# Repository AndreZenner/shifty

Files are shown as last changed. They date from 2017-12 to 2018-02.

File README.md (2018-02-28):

# Shifty
This repository allows you to build your own **Shifty** - a weight-shifting dynamic passiv haptic proxy for virtual reality!

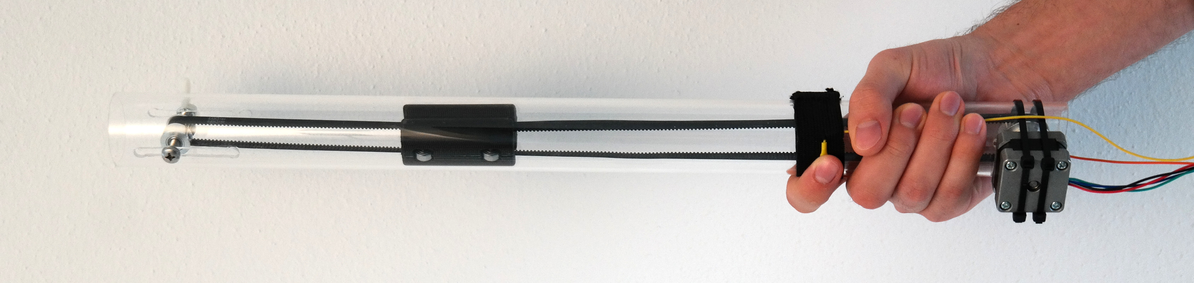
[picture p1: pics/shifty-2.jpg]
Image of the Shifty prototype The Shifty prototype


## Introduction
**Shifty**, as introduced in our TVCG paper [Shifty: A Weight-Shifting Dynamic Passive Haptic Proxy to Enhance Object Perception in Virtual Reality](https://doi.org/10.1109/TVCG.2017.2656978 "Shifty @ IEEE Xplore Digital Library") is a weight-shifting VR controller that allows you to better feel the weight of virtual objects and transformations of them.
For this, it shifts an internal mass while you interact with virtual objects in VR.
Using appropriate visualizations in the virtual environment in synchronization with Shifty's changes in mass distribution (and thus the felt moment of inertia and lever arm), allows for immersive haptic experiences in VR. 

For more information on its haptic effect, the scientific background and user study results, please take a look at the paper.
Shifty was presented at the [IEEE Virtual Reality Conference 2017 in Los Angeles](https://youtu.be/Tzx6ZOIjLhY "Watch the talk!").
To get a first impression, the [corresponding video](https://youtu.be/1l0wKk6q_ss "Watch the video!") is probably a good starting point.

## Reference
```
@article{Zenner:2017:Shifty,
  title={Shifty: A Weight-Shifting Dynamic Passive Haptic Proxy to Enhance Object Perception in Virtual Reality},
  author={Zenner, Andr{\'e} and Kr{\"u}ger, Antonio},
  journal={IEEE Transactions on Visualization and Computer Graphics},
  volume={23},
  number={4},
  pages={1285--1294},
  year={2017},
  publisher={IEEE},
  doi={10.1109/TVCG.2017.2656978}
}
```

## Contents
This repository contains the files, source code and information you need to make your own Shifty prototype.

- [3d-prints](3d-prints/) contains the files to 3D print 
  - Shifty's internal weight hull (you have to fill it with lead granulate)
  - A mount for the HTC Vive tracker (you have to get a 1/4" camera screw) that can be plugged on Shifty
- [circuit](circuit/) contains the [Fritzing](http://fritzing.org/home/) file and a drawing of the used Arduino circuit
- [laser-cut](laser-cut/) contains the .svg cutter file to cut the box holding the electronics
- [pics](pics/) contains pictures of parts, intermediate building steps and the final prototype
- [src](src/) contains the source code
  - [src/arduino](src/arduino/) holds the Arduino firmware to deploy on the Arduino Uno, handling WiFi communication and motor control
  - [src/api](src/api/) holds the C# API that allows programs to talk to Shifty's Arduino and that can be used to control the weight shift and receive button presses. As configured, this Visual Studio project currently builds a .dll to include in your own programs (e.g. used in Unity to communicate with Shifty)
  - [src/unity](src/unity/) holds a small minimal-example project that demonstrates how to integrate the API in Unity using the .dll file (Unity 5.6)
  
## Parts you need
You will probably need the following parts to build the prototype:
- Power:
  - charger for 12V rechargeable battery
  - 12V rechargeable battery (we used a lead accumulator with 7.2 Ah and 6.3mm connectors)
  - DC 12V Step Up Step Down Converter
  - 2x On-Off switch
- Mechanics:
  - plexiglas	pipe outer-Ø: 40,0mm, inner-Ø: 36,0mm
  - Nema 14 Step Motor 12V 0.4A 14Ncm/20oz.in 35x35x26mm 1.8deg Bipolar 4-wire
  - small pulley (GT2 Pulley, 20 teeth, Ø8mm, gear)
  - big pulley (GT2 Pulley, 40 teeth, Ø5mm, gear)
  - toothed belt (GT2)
  - ball bearings for small pulley 5x8x2,5mm
  - ball bearings for weight-wheels 6x12x4mm
  - M5 screw
  - M5 wing nut
  - cable ties for the motor
  - rubberband 25mm width to hold the button
  - velcro strap to fix the rubberband holding the button
  - fine lead granulate ø 0,6 - 1,5 mm
  - backpack to put the battery and electronics in
- Electronics:
  - Arduino Uno R3
  - Adafruit Motor/Stepper/Servo Shield for Arduino Version 2.3
  - Adafruit stacking header set
  - ESP8266 WiFi Module
  - Mini-Breadboard - 400 contacts
  - Mini-Button, placed on Shifty with the rubberband (e.g. SMD Button 3x6x2.5mm)
  - capacitors (104, 100nF)
  - resistors as shown in the circuit schematics
  - LED as shown in the circuit schematics 
  - Buzzer 5V / 12mm
  - shielded microphone cable (4 x 0.14 mm²)
  - connector (8-pin)
  - some jumper wires
  
Additionally, to make the weight and the Vive Tracker mount, you will need access to a 3D printer (we used an Ultimaker 2+; PLA) and to laser-cut the box, access to a laser cutter.

## How-To Build
To build a Shifty prototype, follow these steps:

### Prepare the ESP8266 WiFi chip
We used the ESP8266 module with AT version 0.18 - as it works with the [WeeESP8266](https://github.com/itead/ITEADLIB_Arduino_WeeESP8266) Arduino library. For this to work, you need the corresponding firmware running on your ESP module. To flash the firmware on the module, you can use the [esptool](https://github.com/themadinventor/esptool) and follow [this video](https://www.youtube.com/watch?v=PycRnjcXMRI). A working firmware to flash can be found [here](http://wiki.fablab-nuernberg.de/w/Ding:ESP8266#Firmware) (click V0.9.2.4).
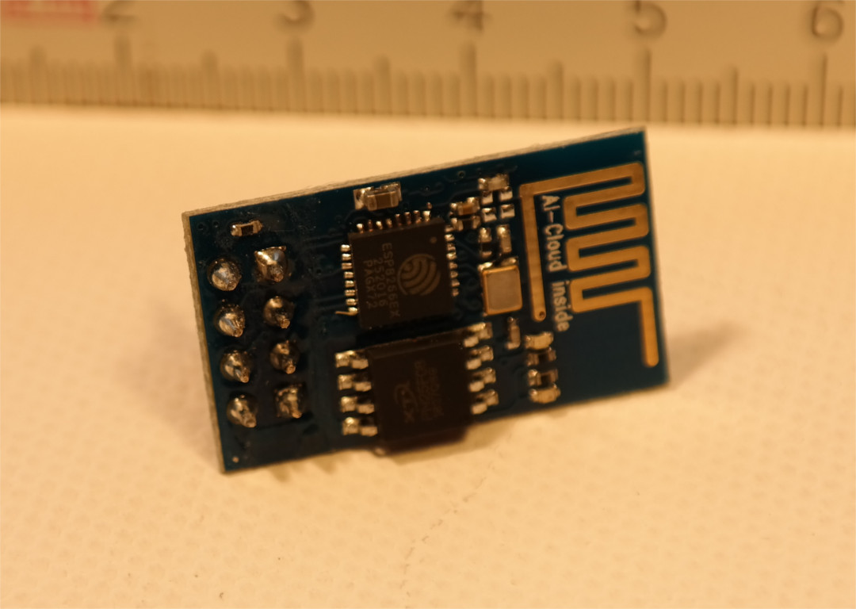
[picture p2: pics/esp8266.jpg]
The ESP8266 WiFi module


### Building Shifty
Having all required parts ready, you can build the prototype:
#### Step 1: Pipe, Motor, Pulley
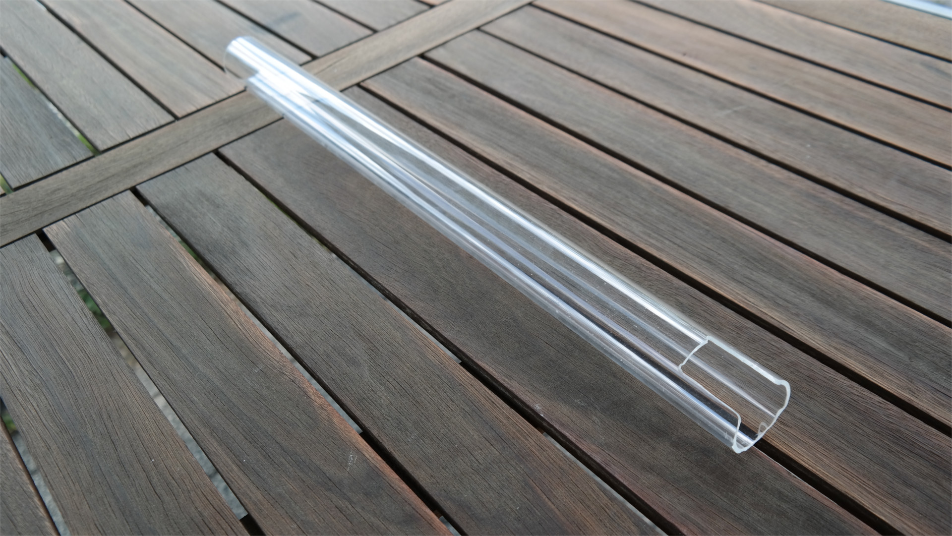
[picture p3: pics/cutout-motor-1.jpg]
motor cutout w/o motor
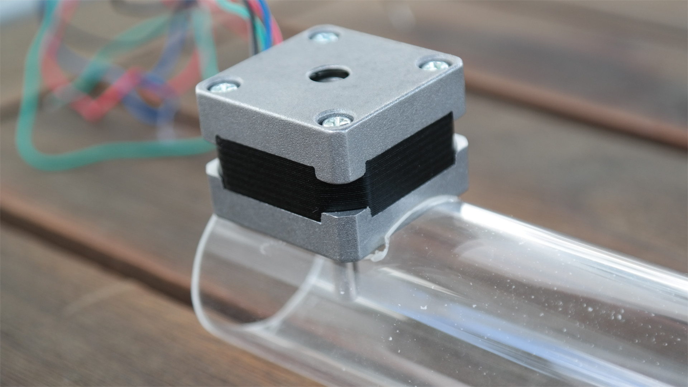
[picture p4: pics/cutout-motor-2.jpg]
motor cutout w/ motor
1. Take the plexiglas pipe, cut it in the desired proxy length and make a cutout for the motor to reside on  
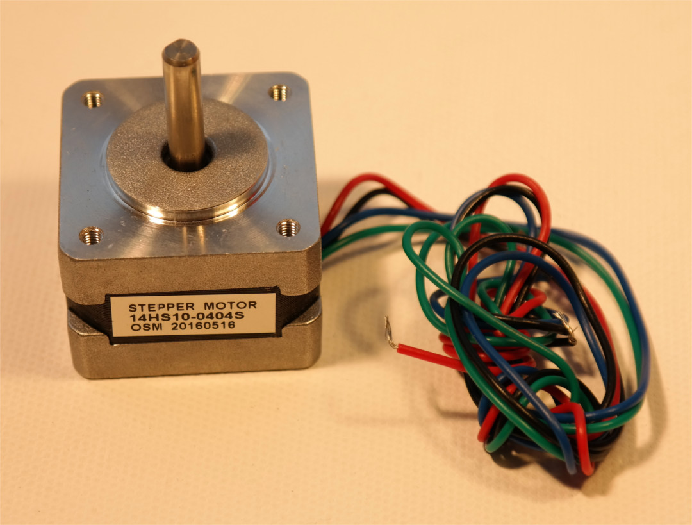
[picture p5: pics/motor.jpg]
motor
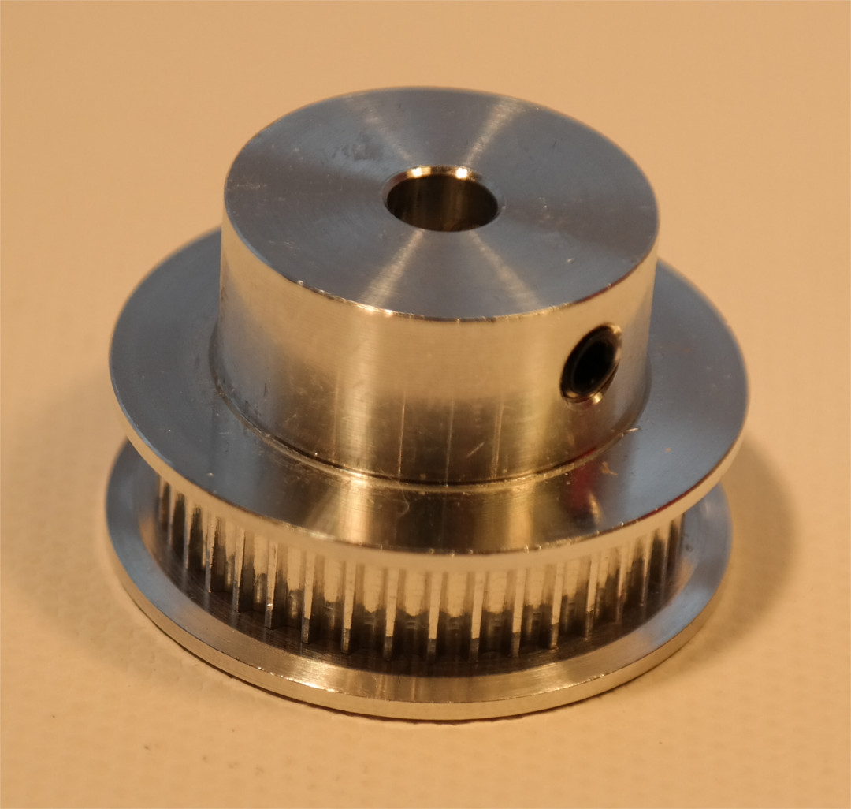
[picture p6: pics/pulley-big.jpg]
big pulley
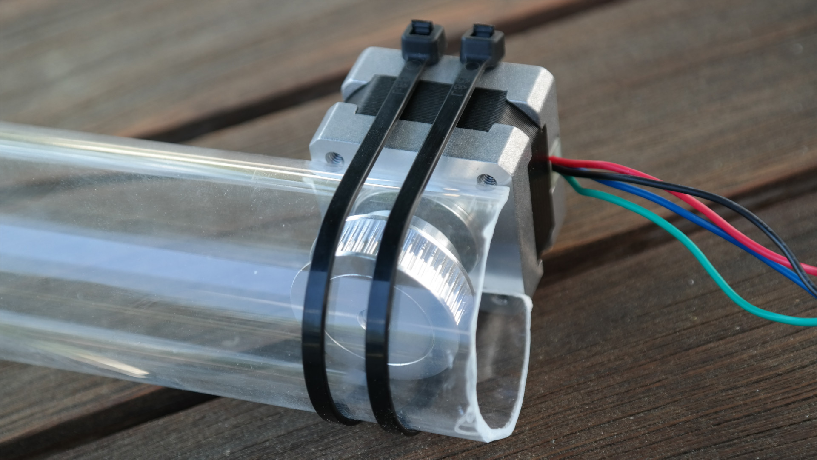
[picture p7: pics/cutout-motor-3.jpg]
motor fixed
2. Using the cable ties, fix the motor with the big pulley screwed on the shaft, so that the pulley is exactly in the center of the pipe. You can put leather between pipe and motor to dampen vibrations and sound.   
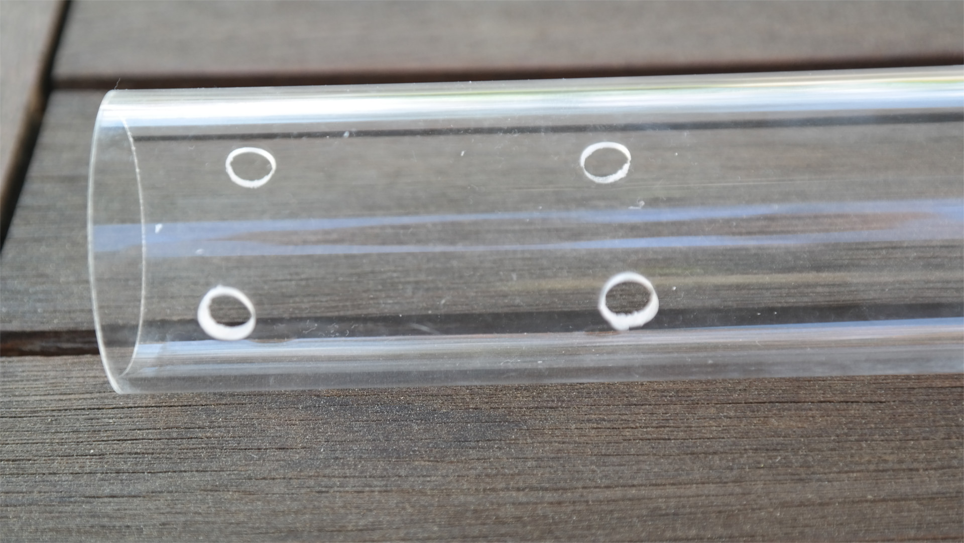
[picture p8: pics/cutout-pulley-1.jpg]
pulley cutout holes
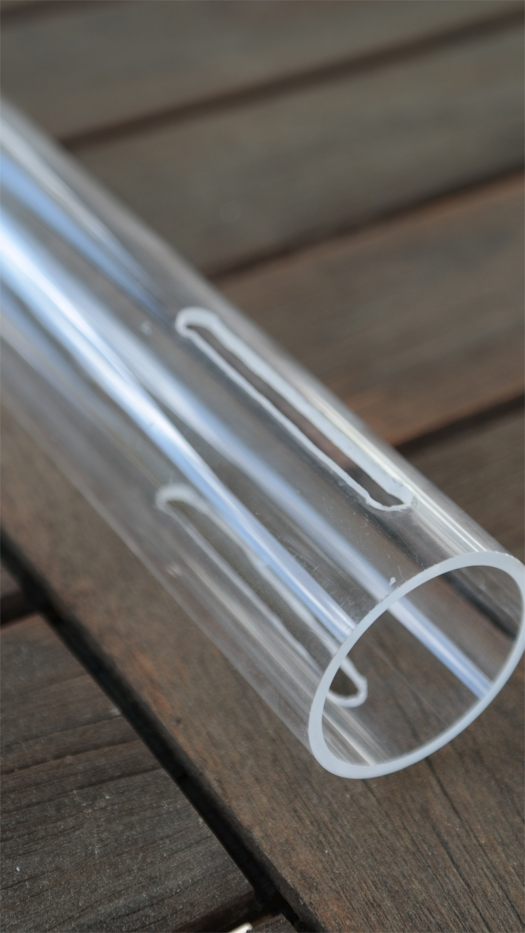
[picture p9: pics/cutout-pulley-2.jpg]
pulley cutout
3. On the other end of the pipe, cut two lengthy recesses for the M5 screw (e.g. by drilling holes and connecting them using a Dremel) 
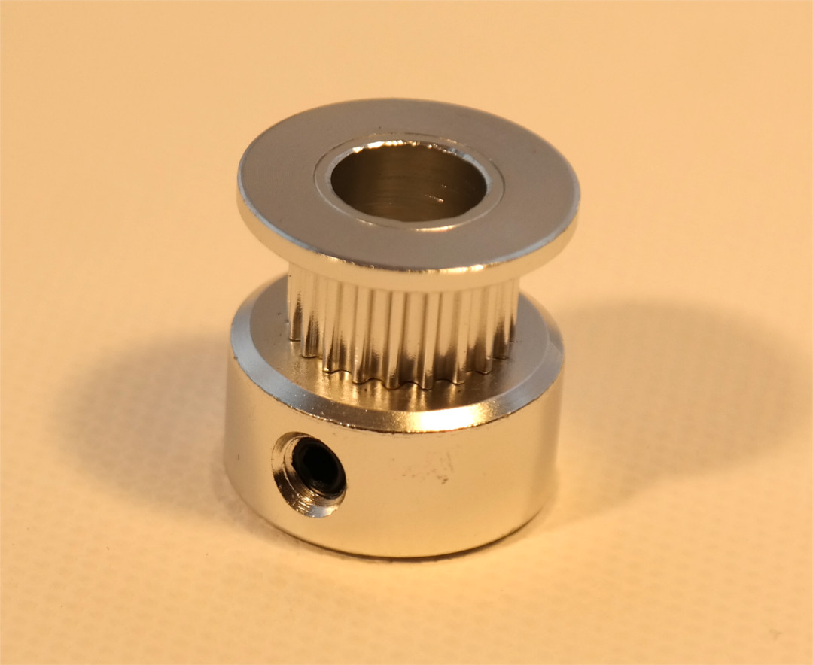
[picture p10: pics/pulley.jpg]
small pulley
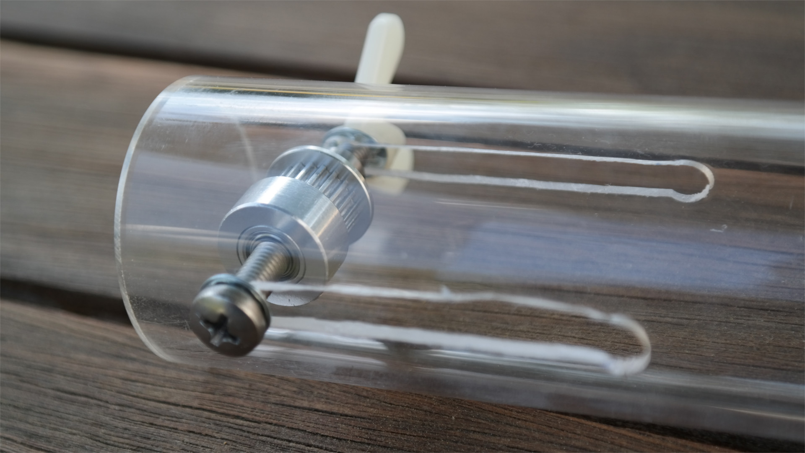
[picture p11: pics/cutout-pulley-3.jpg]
pulley fixed
4. Take the screw, put the small pulley with the ball bearings on it and insert it into the pipe through the recesses. Fix it with the wing nut. 

#### Step 2: Weight, Belt
1. Print the weight hull two times with a 3D printer
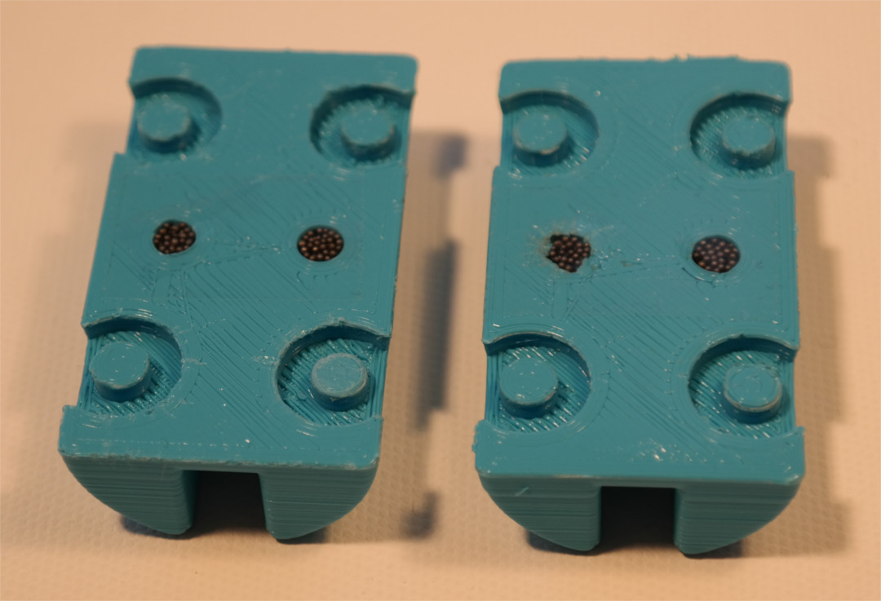
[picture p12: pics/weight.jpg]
2. Fill both halves with the lead granulate 
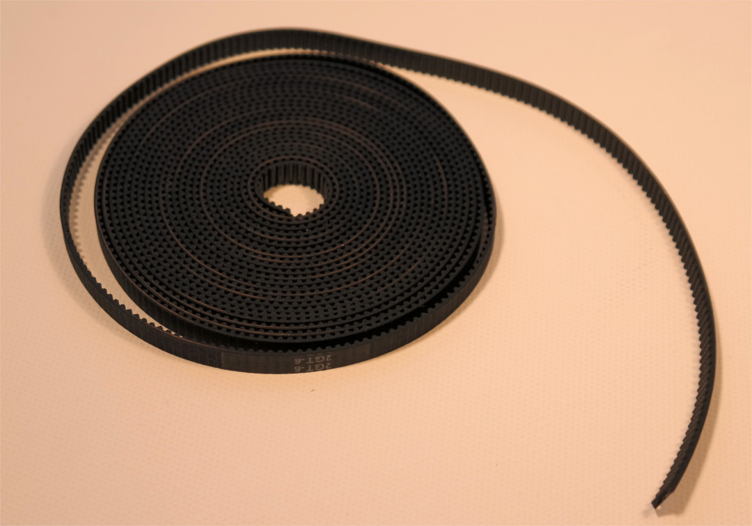
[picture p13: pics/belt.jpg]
belt
3. Measure the distance between the big pulley on the motor and the small pulley on the top end of the pipe to determine the length of the belt. Then cut the belt. 
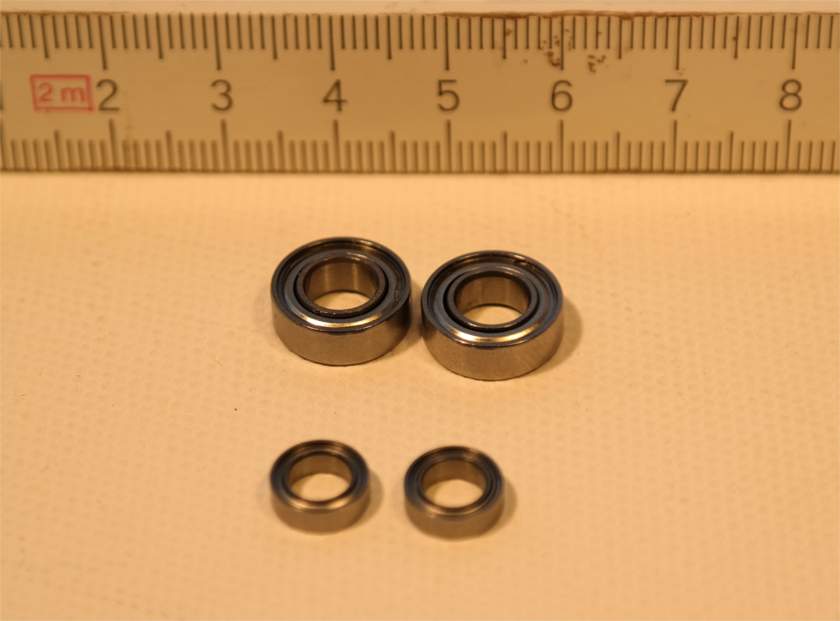
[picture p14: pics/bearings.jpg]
bearings
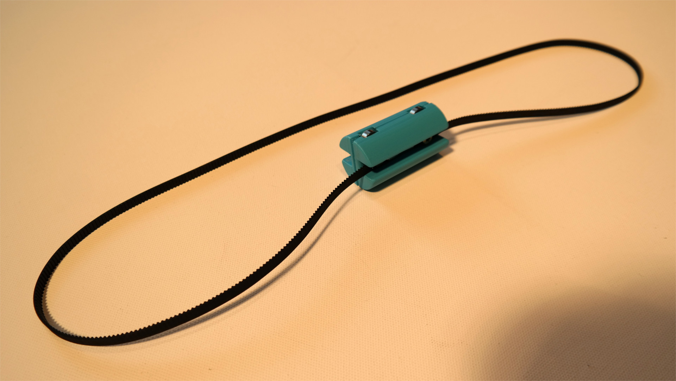
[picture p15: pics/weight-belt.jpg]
assembled weight attached to belt
4. Insert the bearings as weight-wheels and fix the two weight halves. Then attach the belt on the weight.  

#### Step 3: Button
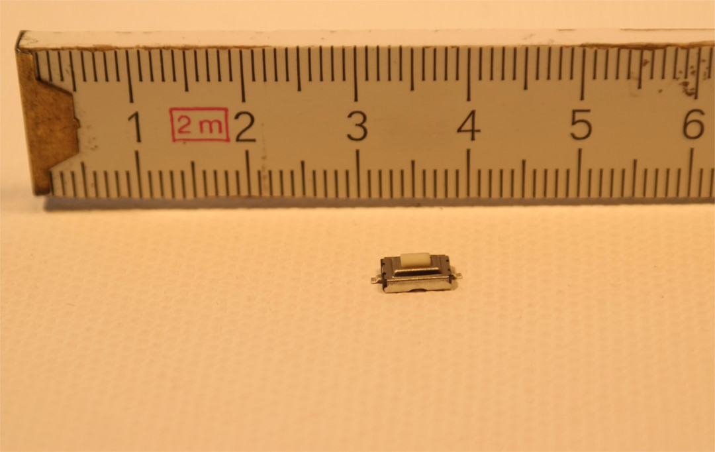
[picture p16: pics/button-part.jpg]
small button
1. Take the small button and attach a cable on both ends. 
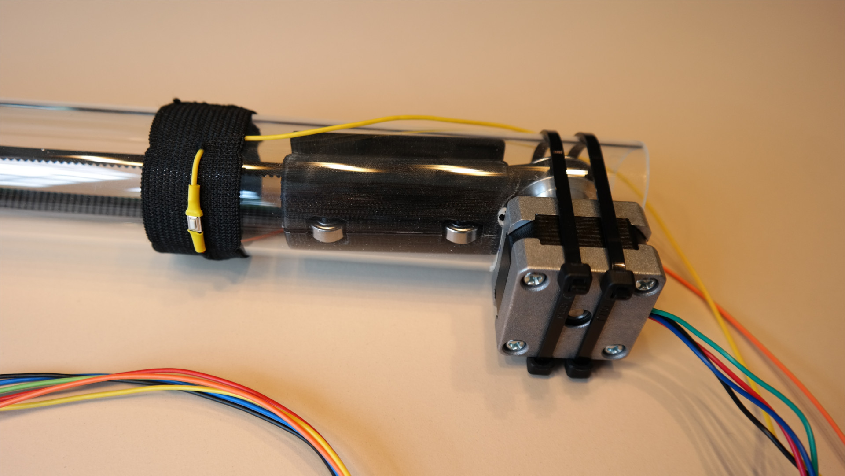
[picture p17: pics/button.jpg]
button fixed with rubberband on Shifty
2. Cut the rubberband and the velcron strap. Stick the two cables through the band in order to attach the button on the pipe. 

#### Step 4: Arduino, Circuit, Cables
1. Prepare the ESP8266 module as described above.
2. Solder the stacking headers to the motor shield and stack the shield on the Arduino.
3. Create the circuit. Shifty circuit
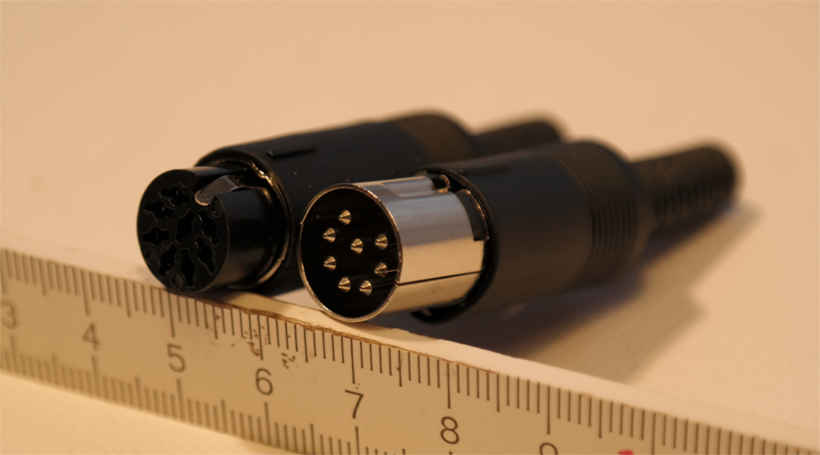
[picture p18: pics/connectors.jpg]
connectors
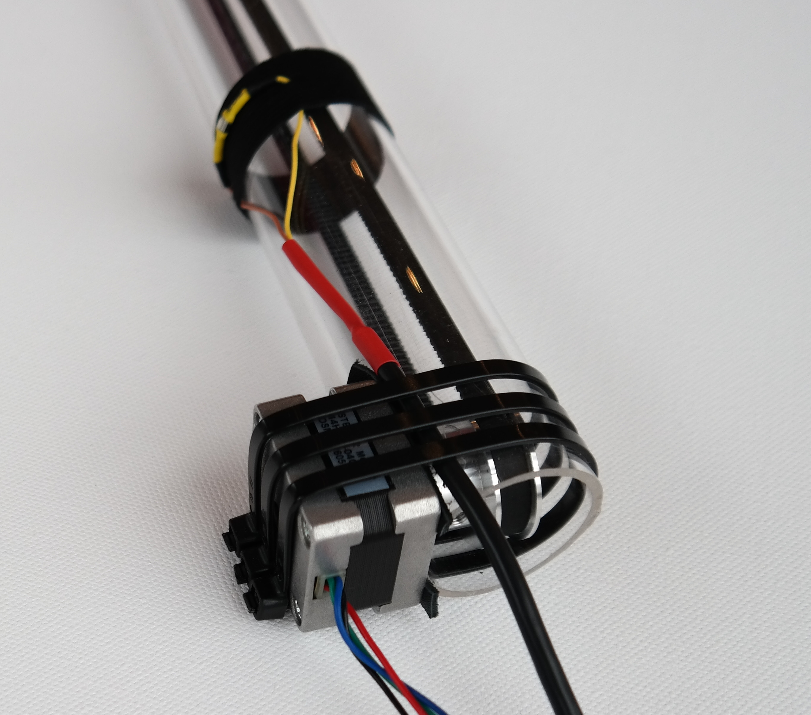
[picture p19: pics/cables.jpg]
cables at Shifty
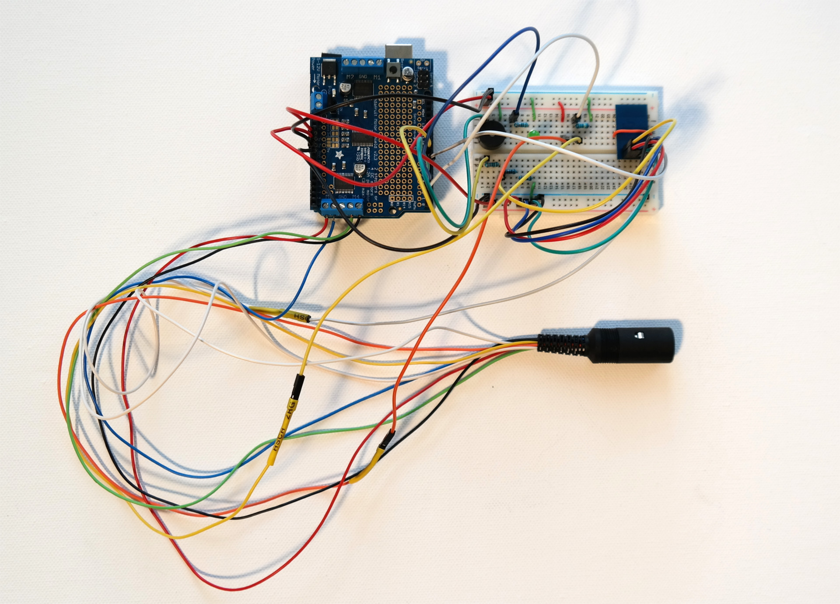
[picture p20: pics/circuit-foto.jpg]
photo of the curcuit
4. Solder the cable connections and connectors. <p>The electronics should look like this:</p>
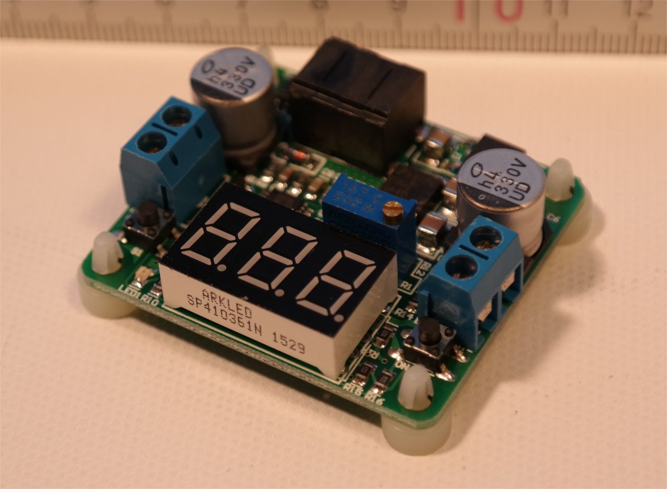
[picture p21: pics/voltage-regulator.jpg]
voltage converter
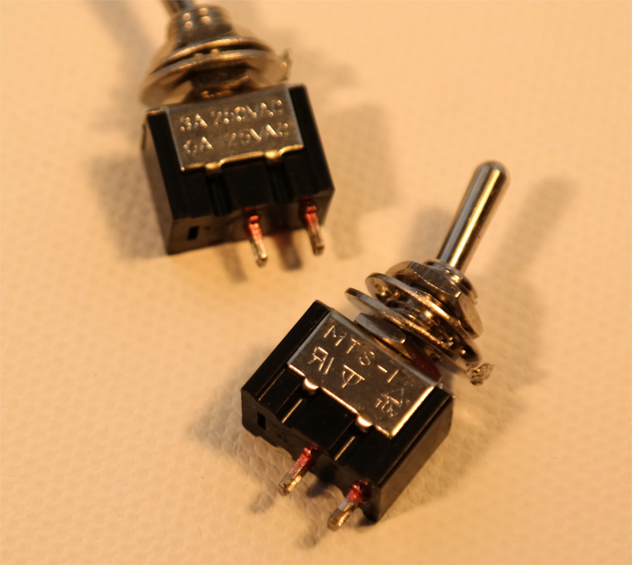
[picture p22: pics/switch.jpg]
switches
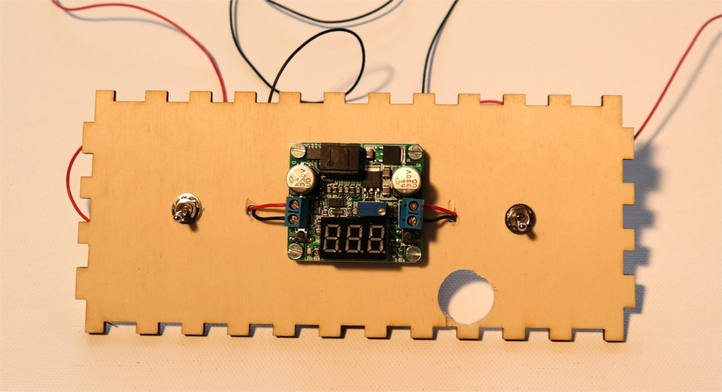
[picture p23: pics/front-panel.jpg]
front panel
5. Using the voltage converter and switches, prepare the power supply (e.g. on the font panel of the box)   

#### Step 5: Final Assembly, Vive Tracker Mount
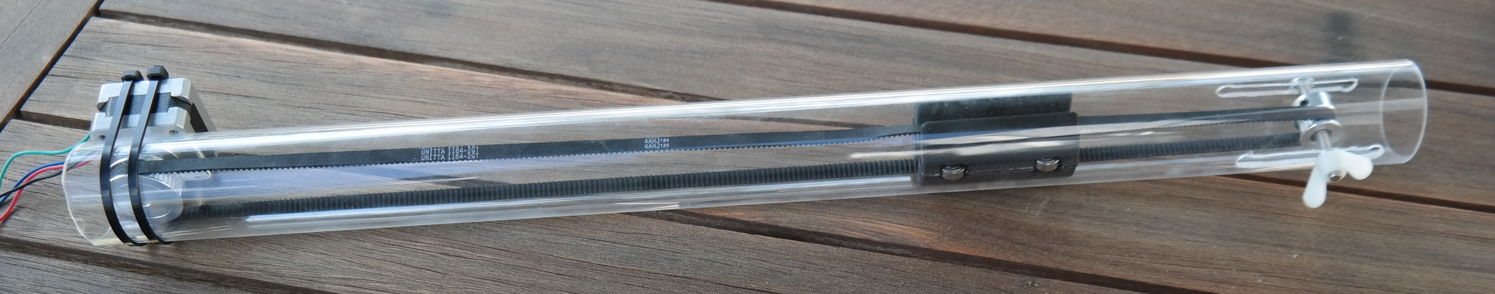
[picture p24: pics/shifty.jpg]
shifty with inserted weight
1. Insert the weight and the belt in the pipe. Fasten the belt by adjusting the position of the top pulley / screw. 
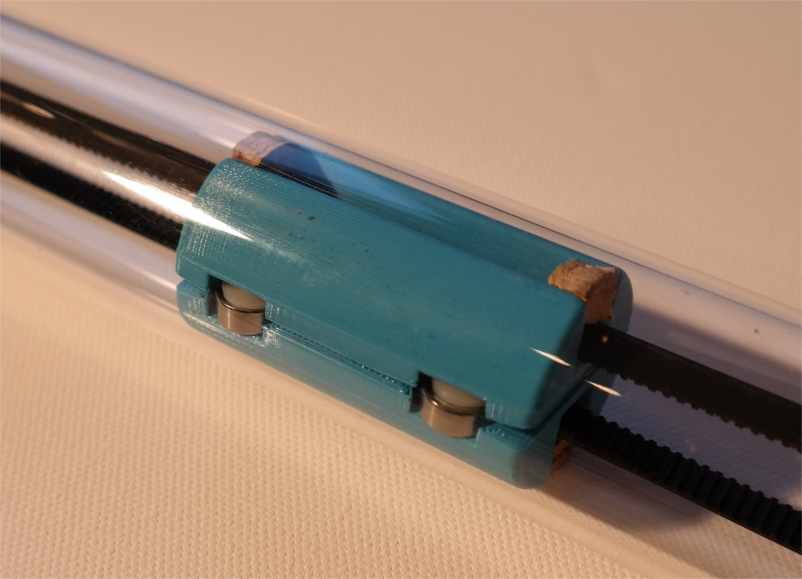
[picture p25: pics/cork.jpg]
cork on the weight
2. If too loud, you can use small pieces of cork to dampen the sound of the internal weight. 
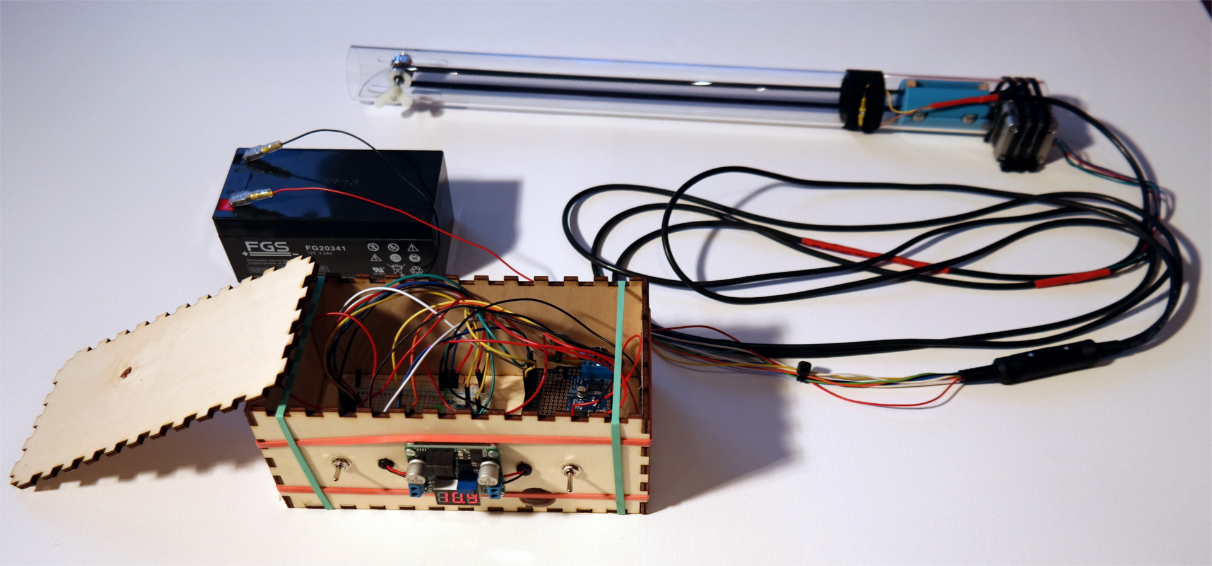
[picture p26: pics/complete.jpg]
complete Shifty prototype
3. Putting everything together, the result should look similar to this: 
4. Deploy the [Shifty Arduino software](src/arduino/) on the Arduino and test if it works. After start-up, Shifty has to be calibrated. For this, the weight will automatically move towards the top and you have to press the button at the top-most end. After that, the weight moves downwards and you have to set the lowest position again by pressing the button. Upon completion of this calibration, Shifty is ready to go!
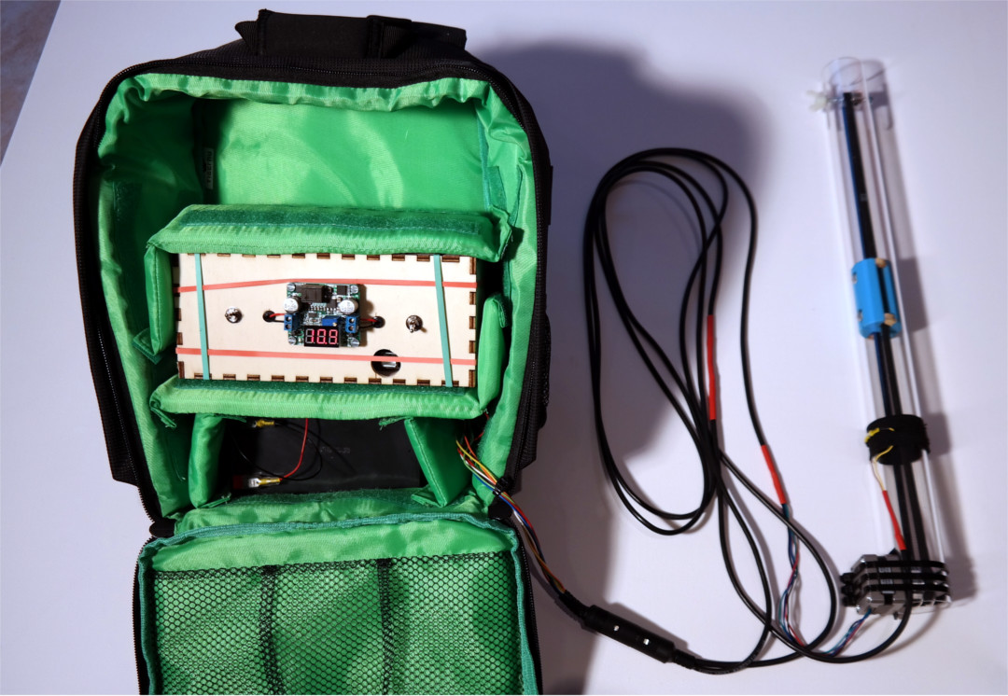
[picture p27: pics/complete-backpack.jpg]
complete Shifty prototype with backpack
5. If everything works, take a backpack and insert the battery and the electronics with the box, just leaving a cable connection to Shifty. Wearing the backback, you can use Shifty even in room-scale VR experiences. 
6. Finally, 3D print the Vive Tracker mount and place the tracker on Shifty to easily track it while in VR.

#### Step 6: Useful Addons
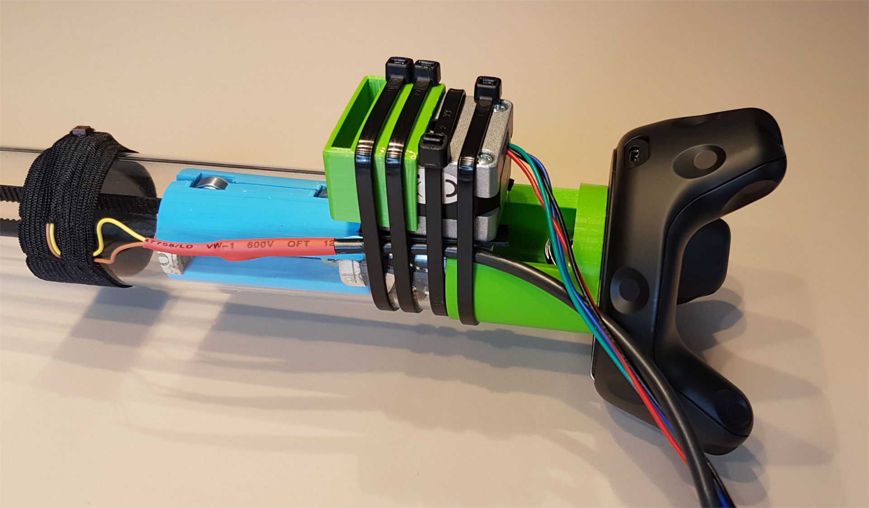
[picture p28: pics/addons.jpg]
3D printed addons

1. For better balance and more ergonomic placement of the Vive tracker, 3D print the grip mount and fix it at the grip end with a cable tie. Screw the Vive tracker with a camera screw.
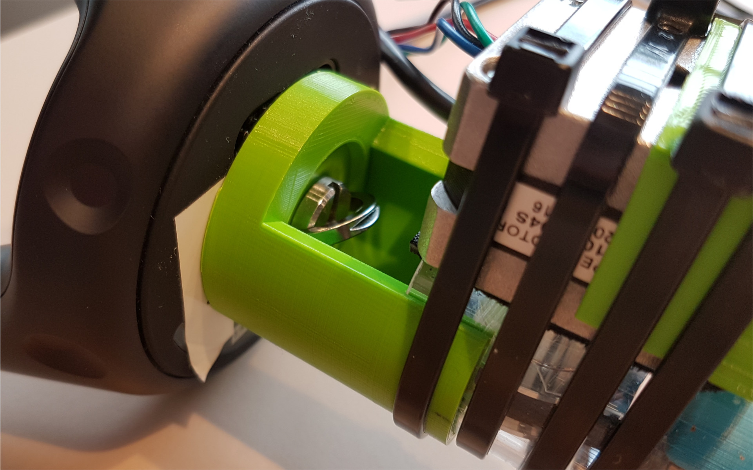
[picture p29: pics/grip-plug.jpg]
the grip mount for the Vive tracker

2. As the motor can become very hot, you should use a heat shield to prevent burning your hand when touching the motor while in VR. For this, you can 3D print the heat shield file and fix it on the motor with additional cable ties.
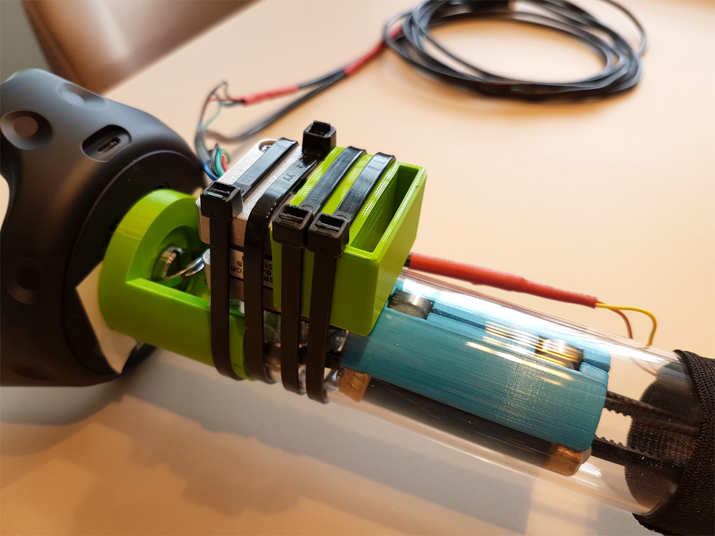
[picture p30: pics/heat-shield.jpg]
heat shield mounted on the motor


### Controlling Shifty
Use the [ProxyControlAPI](src/api/) to connect to Shifty, to pass commands and to read the button states.
The library currently builds a .dll file containing the API functions.
See the [Unity Example](src/unity/), and especially the corresponding [ExampleProxyConnection.cs](src/unity/Shifty-Unity-Minimal-Example/Assets/github-minimal/ExampleProxyConnection.cs) script, as well as the functions offered by the API defined in [ProxyControlAPI.cs](src/api/ProxyControlAPI/ProxyControlClient/ProxyControlAPI.cs), for examples and reference.

To test your prototype, you can build and use the small [ProxyControlAPI-Console tool](src/api/ProxyControlAPI/) that allows you to send commands manually in order to test your device.

## Credits
Before use, please see the [LICENSE](LICENSE.md) for copyright and license details.

Authors of the [paper](https://doi.org/10.1109/TVCG.2017.2656978 "Shifty @ IEEE Xplore Digital Library"):  
**André Zenner** - andre.zenner@dfki.de  
**Prof. Dr. Antonio Krüger** - krueger@dfki.de

This work was supported by the [Deutsches Forschungszentrum für Künstliche Intelligenz GmbH](https://www.dfki.de/) (DFKI; German Research Center for Artificial Intelligence) and [Saarland University](https://www.uni-saarland.de/).
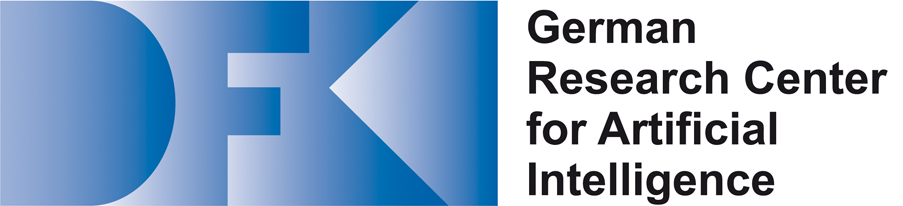
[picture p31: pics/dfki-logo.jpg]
DFKI Logo

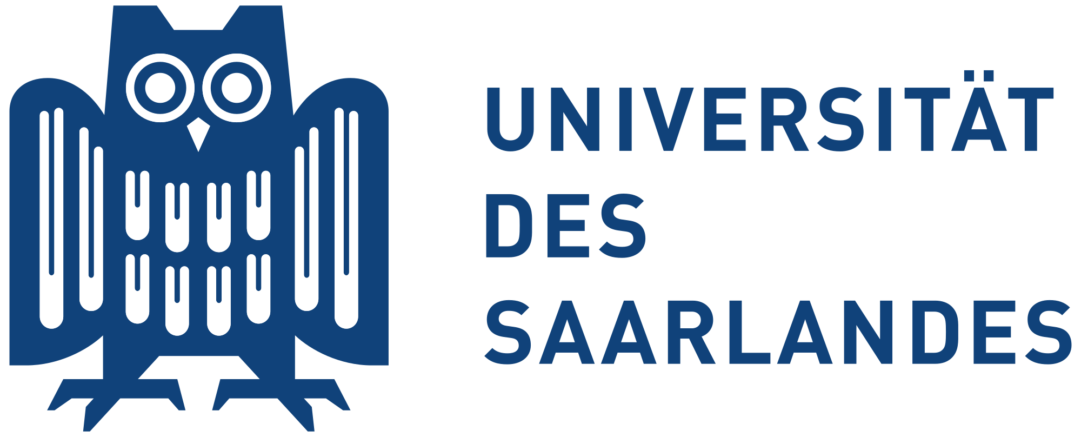
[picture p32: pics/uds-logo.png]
Saarland University Logo


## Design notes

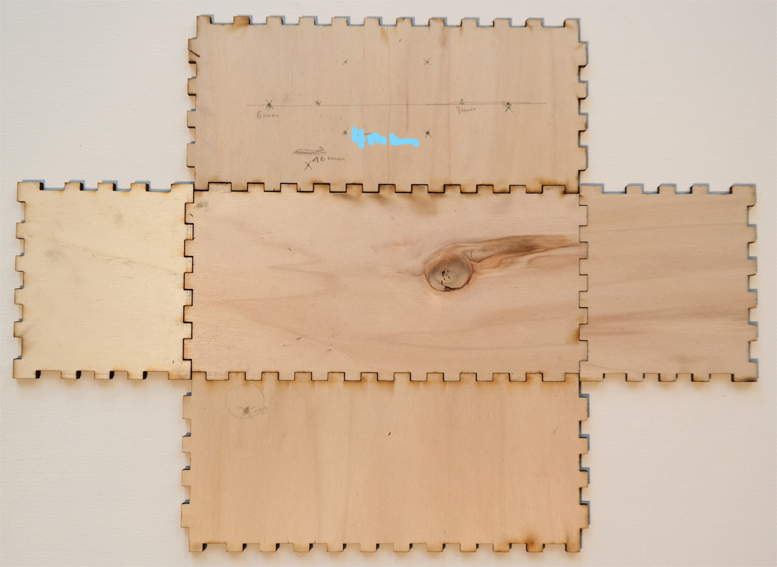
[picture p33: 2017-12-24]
pics/box-1.jpg

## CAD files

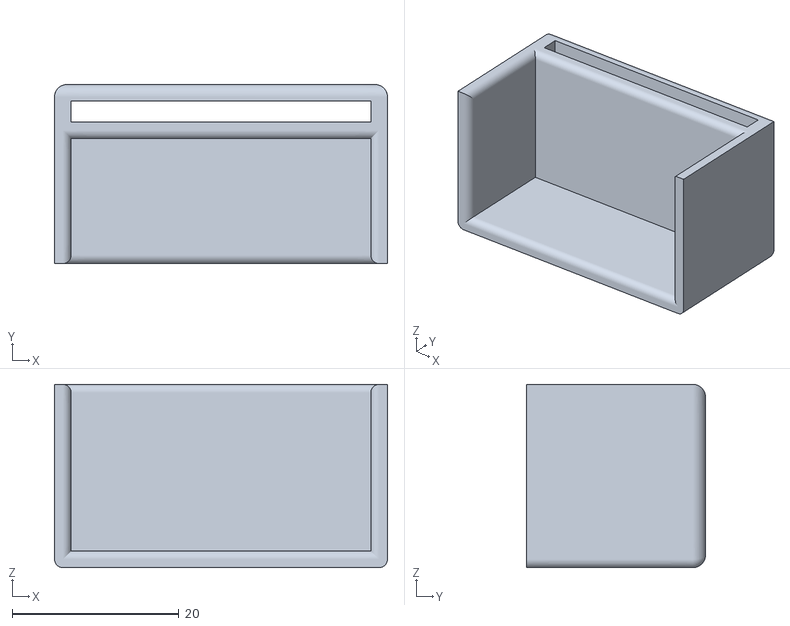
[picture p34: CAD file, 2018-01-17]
3d-prints/v2-Shifty-Heat-Shield.stl
40.0 x 21.5 x 22.0

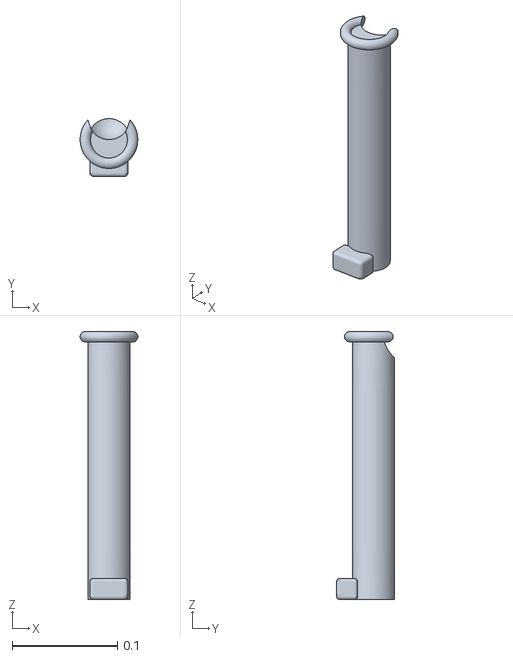
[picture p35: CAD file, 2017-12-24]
src/unity/Shifty-Unity-Minimal-Example/Assets/VirtualObjects/grip1.obj
0.0549 x 0.055 x 0.255

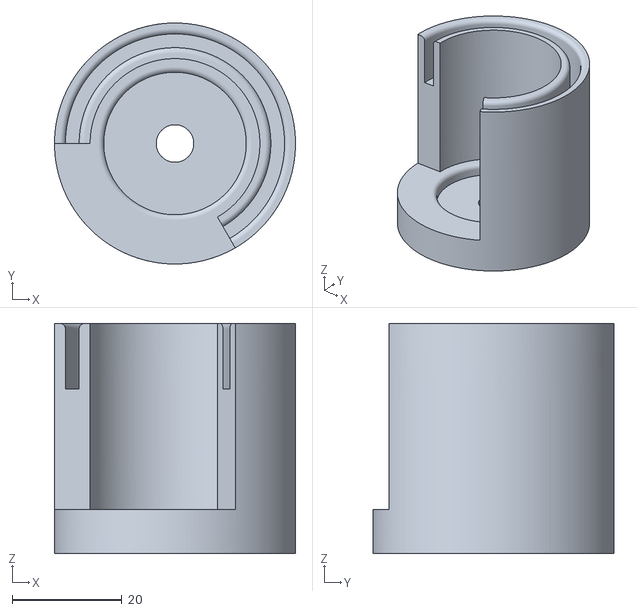
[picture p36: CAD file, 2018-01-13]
3d-prints/v2-Shifty-Grip-Vive-Tracker-Plug.stl
44.0 x 44.0 x 42.0

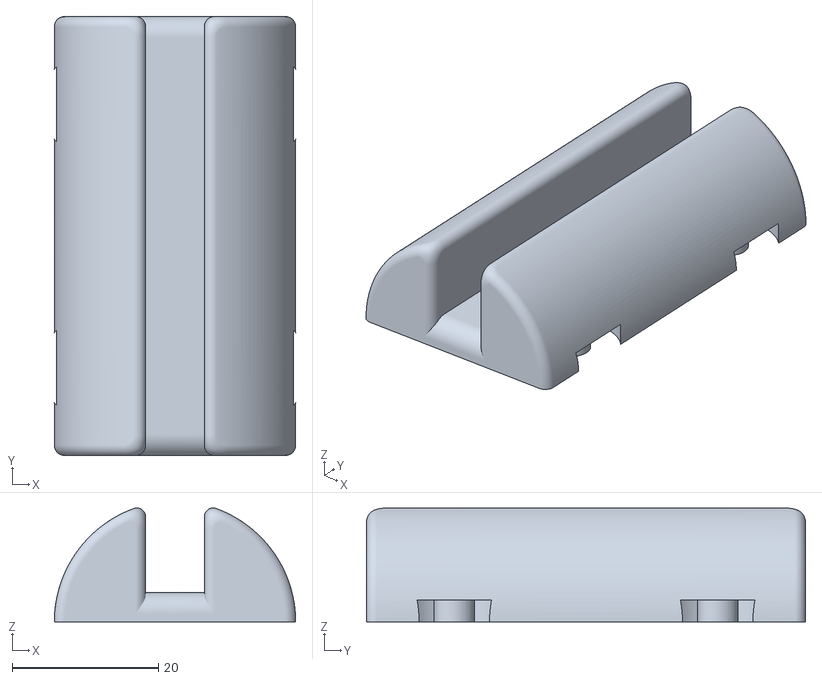
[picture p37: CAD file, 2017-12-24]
3d-prints/v37-Proxy-Weight-Version-1-radius16.5mm-length60mm.obj
33.0 x 60.0 x 15.6

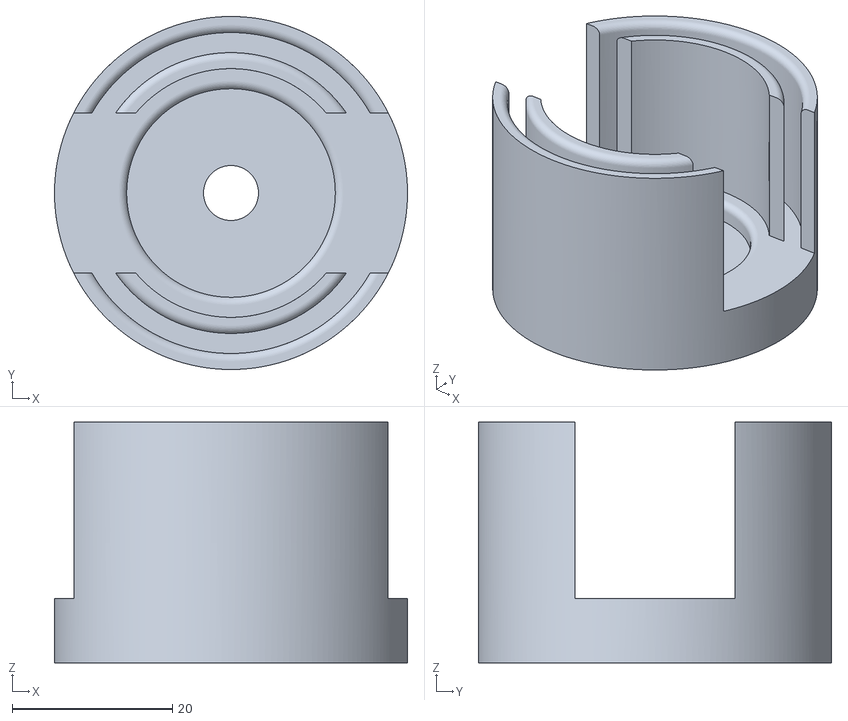
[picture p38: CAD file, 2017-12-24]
3d-prints/v9-Shifty-Vive-Tracker-Plug.stl
44.0 x 44.0 x 30.0

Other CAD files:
3d-prints/v2-Shifty-Grip-Vive-Tracker-Plug.f3d
3d-prints/v2-Shifty-Grip-Vive-Tracker-Plug.obj
3d-prints/v2-Shifty-Heat-Shield.f3d
3d-prints/v2-Shifty-Heat-Shield.obj
3d-prints/v37-Proxy-Weight-Version-1-radius16.5mm-length60mm.f3d
3d-prints/v9-Shifty-Vive-Tracker-Plug.f3d
3d-prints/v9-Shifty-Vive-Tracker-Plug.obj

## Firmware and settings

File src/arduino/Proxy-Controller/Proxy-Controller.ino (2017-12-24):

/*
 * The Proxy-Controller Software
 * 
 * Author: André Zenner
 * 
 * 
 * USED LIBRARIES:
 *    * AccelStepper (Adafruit fork to support MotorShield v2.3 https://github.com/adafruit/AccelStepper
 *    * Adafruit MotorShield v2 Library https://github.com/adafruit/Adafruit_Motor_Shield_V2_Library
 *    * WeeESP8266 Library by itead for the WiFi functionality https://github.com/itead/ITEADLIB_Arduino_WeeESP8266
 *    * Standard Arduino Libraries (SoftwareSerial, ...)
 */

/*-----( Import needed libraries )-----*/
#include "Proxy.h"
#include "ProxyControlServer.h"


/*-----( Declare Constants and Pin Numbers )-----*/
//PROXY-CONTROLLER
#define VERSION 17
#define USE_WIFI true
#define CONNECT_TO_WIFI true
#define ENABLE_BUTTON true

//MOTOR CONTROL                   
#define motorPort 2
#define motorStepsPerRevolution 200

//WIFI
#define SSID        "WIFINAME1"
#define PASSWORD    "WIFIPASSWORD1"
#define SSID2       "WIFINAME2"
#define PASSWORD2   "WIFIPASSWORD2"

//USER INPUT
#define buttonPin 2

//USER OUTPUT
#define LEDPin 3
#define buzzerPin 4


/*-----( Declare objects )-----*/
//Declarations of functions passed to other parts of the system
void beep(int mil);
void light(int mil);

// NEMA 14: stepper motor with 200 steps per revolution (1.8 degree)
// connected to motor port #2 (M3 and M4)
Proxy proxy(motorStepsPerRevolution, motorPort, DOUBLE, ENABLE_BUTTON ? buttonPin : 0, &beep, &light);
ProxyControlServer server;


/*-----( Declare Variables )-----*/
//none

void setup()   /****** SETUP: RUNS ONCE ******/
{
  Serial.begin(9600);
  Serial.println(F("\nProxy-Controller initializing ...\n"));

  /* VERSION INFO */
  Serial.print(F("\tProxy Firmware Version: v"));
  Serial.println(VERSION);
  
  /* INIT USER I/O */
  Serial.println(F("\tUser I/O initializing ..."));
  pinMode(buttonPin, INPUT);
        //DEBUG
        //attachInterrupt(digitalPinToInterrupt(buttonPin), onInterrupt, CHANGE);
        //END DEBUG
  pinMode(LEDPin, OUTPUT);
  pinMode(buzzerPin, OUTPUT);
  tone(buzzerPin, 261, 100);
  Serial.println(F("\tUser I/O initialized!"));

  /* INIT MOTOR */
  proxy.init();
  
  /* INIT WIFI */
  if(USE_WIFI){
    bool initialPress = (digitalRead(buttonPin) == HIGH);
    if(initialPress){
      tone(buzzerPin, 800, 1000);
      delay(2000);
    }
    //bool connectWifi = CONNECT_TO_WIFI && !initialPress;
    String ssid = initialPress ? SSID2 : SSID;
    String password = initialPress ? PASSWORD2 : PASSWORD;
    server.init(CONNECT_TO_WIFI, ssid, password, 8090, 7200, &proxy, VERSION, &beep, &light);
    server.startServer();
  }else{
    Serial.println(F("\tSkipping WiFi according to configuration"));
  }
  
  notifyReady();
  Serial.println(F("Proxy-Controller initialized!\n\n"));

  /* START INITIAL CALIBRATION */
  proxy.calibrationStart();  

}//--(end setup )---

//DEBUG
void onInterrupt(){
  Serial.println(analogRead(buttonPin));  
}
//END DEBUG


void loop()   /****** LOOP: RUNS CONSTANTLY ******/
{

  /* USER I/O */
  if(buttonPressed(buttonPin) && proxy.calibrating() != CALIBRATION_PHASE_NONE){
    if(proxy.calibrating() == CALIBRATION_PHASE_UP){
      tone(buzzerPin, 800, 100);
      delay(500);
      proxy.calibrationMaximumReached();
    }else if(proxy.calibrating() == CALIBRATION_PHASE_DOWN){
      proxy.calibrationMinimumReached();
      tone(buzzerPin, 800, 100);
      delay(200);
      tone(buzzerPin, 800, 100);
      delay(200);
      delay(2000);
    }
  }
  
  if(ENABLE_BUTTON && proxy.calibrating() == CALIBRATION_PHASE_NONE){
    int buttonEvent = proxy.getButtonEvent();
    if(buttonEvent != BUTTON_EVENT_NONE){
      proxy.stopNow();
      server.sendButtonEvent(server.getLastMuxID(), buttonEvent, proxy.getCurrentPosition()); 
      //if(buttonEvent == BUTTON_EVENT_DOWN){
      //  proxy.savePower();
      //}
    }
  }
  
  /* WIFI */
  if(USE_WIFI && !proxy.operating()){
    server.listenForCommands();
  }

  /* MOTOR */
  proxy.go();
  
}//--(end main loop )---



/*-----( Declare User-written Functions )-----*/

/* Blinks the LED x times for y millies */
void blink(int ledPin, int times, int mil){
  for(int i=0; i<times; i++){
    digitalWrite(ledPin, HIGH);
    delay(mil);
    digitalWrite(ledPin,LOW);
    delay(mil);
  }
}

bool buttonPressed(int pin){
  int buttonState = digitalRead(pin);
  delay(1);
  int buttonState2 = digitalRead(pin);
  return buttonState == buttonState2 && buttonState == HIGH;
}

void notifyReady() {
  tone(buzzerPin, 261, 100);
  blink(LEDPin, 3, 100);
  tone(buzzerPin, 523, 100);
  delay(100);
  tone(buzzerPin, 523, 100);
}

//to be passed to other system parts
void beep(int mil){
  tone(buzzerPin, 261, mil);
}

//to be passed to other system parts
void light(int mil){
  if(mil == -1){
    digitalWrite(LEDPin, LOW);
  }else if(mil == 0){
    digitalWrite(LEDPin, HIGH);
  }else{
    blink(LEDPin, 1,mil);
  }
}

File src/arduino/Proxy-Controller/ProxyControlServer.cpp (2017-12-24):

/*
  ProxyControlServer.cpp - A TCP server that allows to control the proxy object remotely via a simple WiFi protocol.
  Created by André Zenner, April 30, 2016.
*/

#include "Arduino.h"
#include "ProxyControlServer.h"

#define PROTOCOL_PACKET_SIZE 5

ProxyControlServer::ProxyControlServer() : _wifi(_serial1) {
  _serial1.begin(9600);
}

void ProxyControlServer::init(bool connectToWifi, String ssid, String pw, int port, int timeout, Proxy* proxy, float versioninfo, void (*beep)(int), void (*light)(int)) {
  if (proxy == NULL) {
    Serial.print(F("ERROR: ProxyControlServer initialized with 'NULL' Proxy pointer!"));
  }
  _ssid = ssid;
  _pw = pw;
  _proxy = proxy;
  _port = port;
  _timeout = timeout;
  _commandsReceived = 0;
  _beep = beep;
  _light = light;
  _version = versioninfo;

  /* INIT WIFI */
  bool initSuccess = true;
  Serial.print(F("\tESP8266-WiFi Module AT Version:"));
  Serial.println(_wifi.getVersion().c_str());

  if (_wifi.setOprToStationSoftAP()) {
    Serial.print(F("\tOperation Mode set to 'station + softap' ... OK\r\n"));
    initSuccess &= true;
  } else {
    Serial.print(F("\tOperation Mode set to 'station + softap' ... ERROR\r\n"));
    initSuccess &= false;
    _beep(200);
    delay(200);
    _beep(200);
    delay(200);
    _beep(400);
  }

  if (connectToWifi) {
    if (_wifi.joinAP(_ssid, _pw)) {
      Serial.println(_ssid);
      Serial.print(F("\tJoined WiFi Network ... SUCCESS\r\n"));
      initSuccess &= true;
    } else {
      Serial.println(_ssid);
      Serial.print(F("\tJoined WiFi Network ... ERROR\r\n"));
      initSuccess &= false;
    }
  } else {
    Serial.print(F("\tWiFi Network opened! Not joining external WiFi Network according to configuration!\r\n"));
    initSuccess &= true;
  }

  Serial.print(F("\tIP: "));
  Serial.println(_wifi.getLocalIP().c_str());


  if (_wifi.enableMUX()) {
    Serial.print(F("\tEnabled 'multi-client' Mode ... SUCCESS\r\n"));
    initSuccess &= true;
  } else {
    Serial.print(F("\tEnabled 'multi-client' Mode ... ERROR\r\n"));
    initSuccess &= false;
  }

  if (initSuccess) {
    Serial.print(F("\t\t--> WiFi Module ready!\n\n"));
  } else {
    Serial.print(F("\t\t--> Error initializing WiFi Module!\n\n"));
  }
}


bool ProxyControlServer::startServer() {
  bool startServerSuccess = true;
  if (_wifi.startTCPServer(_port)) {
    Serial.print(F("\tPort: "));
    Serial.print(_port);
    Serial.print(F("\n"));
    Serial.print(F("\tStarting TCP Server ... SUCCESS\r\n"));
    startServerSuccess &= true;
  } else {
    Serial.print(F("\tStarting TCP Server ... ERROR\r\n"));
    startServerSuccess &= false;
  }

  if (_wifi.setTCPServerTimeout(_timeout)) {
    Serial.print(F("\tSet TCP Server Timeout to "));
    Serial.print(_timeout);
    Serial.print(F(" seconds ... SUCCESS\r\n"));
    startServerSuccess &= true;
  } else {
    Serial.print(F("\tSet TCP Server Timeout to "));
    Serial.print(_timeout);
    Serial.print(F(" seconds ... ERROR\r\n"));
    startServerSuccess &= false;
  }

  if (startServerSuccess) {
    Serial.println(F("\t\t--> Ready to receive remote commands!\n\n"));
  } else {
    Serial.println(F("\t\t--> Could not start TCP server correctly!\n\n"));
  }
}

bool ProxyControlServer::listenForCommands() {
  uint8_t buffer[PROTOCOL_PACKET_SIZE] = {0};
  uint8_t mux_id;
  uint32_t len = _wifi.recv(&mux_id, buffer, sizeof(buffer), 100);   //do not use a long timeout here (maybe 100), as button presses will be checked at this frequency
  if (len > 0) {
    Serial.print(F("\tReceived data from remote ("));
    Serial.print(mux_id);
    Serial.print(F("):"));
    _lastMuxID = mux_id;
    //Serial.print(F("["));
    //Serial.print(_wifi.getIPStatus().c_str());
    //Serial.println(F("]"));

    Serial.print(F("\t\t--> ["));
    for (uint32_t i = 0; i < PROTOCOL_PACKET_SIZE; i++) {
      Serial.print((char)buffer[i]);
    }
    Serial.print(F("]\r\n"));

    //correct protocol package
    if (len == 5) {
      uint8_t command = buffer[0];
      float payload = *((float*)(&(buffer[1])));

      Serial.print(F("\t\t--> ["));
      Serial.print(command);
      Serial.print(F(", "));
      Serial.print(payload, 8);
      Serial.print(F("]\r\n)"));

      handleCommand(mux_id, command, payload);

      //Serial.print(F("Server Status:["));
      //Serial.print(_wifi.getIPStatus().c_str());
      //Serial.println(F("]"));

    } else {
      Serial.println(F("\t\t--> Data is not protocol conform!"));
    }

    Serial.print(F("\n\n"));
  }
}

/* handling the protocol */
void ProxyControlServer::handleCommand(uint8_t mux_id, uint8_t command, float payload) {

  if (command == 0) { //client requested current position
    Serial.print(F("\t-> Client requested current position ..."));
    if (_light != NULL)
      _light(5);
    _commandsReceived++;
    float retPayload = _proxy->getCurrentPosition();
    sendResponse(mux_id, command, retPayload);
    Serial.println(F(" sent!"));

  } else if (command == 1) { //client sends new target position
    Serial.println(F("\t-> Client sends new target position!"));
    if (_light != NULL)
      _light(2);
    _commandsReceived++;
    sendResponse(mux_id, command, _proxy->getExpectedTimeTo(payload));
    _proxy->setTargetPosition(payload);
    Serial.println(F("\t-> ACK sent!"));

  } else if (command == 2) {
    Serial.println(F("\t-> Client sends new speed ..."));
    if (_light != NULL)
      _light(2);
    _commandsReceived++;
    sendResponse(mux_id, command, *((float*)(&"OK")));
    _proxy->setCurrentSpeed((int) payload);
    Serial.println(F("\t-> ACK sent!"));

  } else if (command == 3) {
    Serial.println(F("\t-> Client requests isTargetReached ..."));
    if (_light != NULL)
      _light(5);
    _commandsReceived++;
    float retPayload = _proxy->isTargetReached() ? 1 : 0;
    sendResponse(mux_id, command, retPayload);
    Serial.println(F(" sent!"));

  } else if (command == 4) {
    Serial.println(F("\t-> Client requests current speed ..."));
    if (_light != NULL)
      _light(5);
    _commandsReceived++;
    float retPayload = (float) _proxy->getCurrentSpeed();
    sendResponse(mux_id, command, retPayload);
    Serial.println(F(" sent!"));

  } else if (command == 5) {
    Serial.println(F("\t-> Client requests recalibration ..."));
    if (_light != NULL)
      _light(2);
    if (_beep != NULL) {
      _beep(200);
      delay(400);
      _beep(200);
    }
    _commandsReceived++;
    sendResponse(mux_id, command, *((float*)(&"OK")));
    _proxy->calibrationStart();
    Serial.println(F("\t-> ACK sent!"));

  } else if (command == 6) {
    Serial.println(F("\t-> Client requests expected time ..."));
    if (_light != NULL)
      _light(5);
    _commandsReceived++;
    float retPayload = _proxy->getExpectedTimeTo(payload);
    sendResponse(mux_id, command, retPayload);
    Serial.println(F("\t-> Time sent!"));
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

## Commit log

2017-12-24 initial commit incl. 3d-print files, circuit info, laser-cutter file, pics, source (api, arduino, unity example). - License added.
    [grip1.obj, shifty-circuit.fzz, v37-Proxy-Weight-Version-1-radius16.5mm-length60mm.f3d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]
2018-01-13 vive-tracker plug for the grip added
    [v2-Shifty-Grip-Vive-Tracker-Plug.f3d, v2-Shifty-Grip-Vive-Tracker-Plug.obj, v2-Shifty-Grip-Vive-Tracker-Plug.stl]
2018-01-17 heat-shield 3D print files added. pictures added.
    [v2-Shifty-Heat-Shield.f3d, v2-Shifty-Heat-Shield.obj, v2-Shifty-Heat-Shield.stl]
